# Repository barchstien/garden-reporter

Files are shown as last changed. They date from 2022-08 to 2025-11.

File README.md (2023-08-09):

[TOC]

# Overview
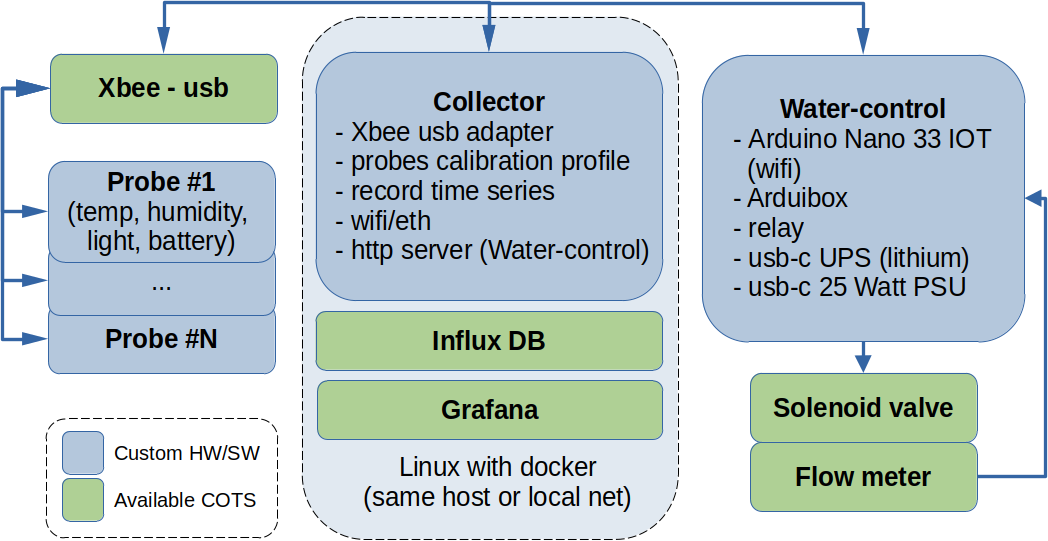
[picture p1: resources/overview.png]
probe overview


Collect data about the garden (soil humidity, luminosity and temperature), that is gathered via xbee link to the collector, for storage and visualisation.

Control and measure water flow. It flows when it is programmed to, or when manually triggered for a set duration.

Xbee modules are configured to :
 - cycle sleep to probe every 15min and stay ON for around 100 msec
 - send data to the collector

## UI and Configuration
 * Collector is configured via YAML, see [collector](/collector/) folder
 * Probes are configured when deployed, by uploading the profile (see profile*.xpro files)
 * Visulisation via Grafana
 * Water-control polls the set program every time it reports water flow
 * Water flow program is configured via web UI

# Probe
More doc about probe in [probe/](/probe)

# Collector
More doc about collector in [collector/](/collector)

# Water-control
More doc about water-control in [water-control/](/water-control)

# grafana-dashboards
Collection of grafan dashboards, exported as JSON, [here](/grafana-dashboards)

# resources
Images and diagrams

# IRL
The system has been running as a prototype since autumn 2022. Thought, after 2 months, the deployed probes started to randomly block, ie not wake up anymore, until it was rebooted. It got fixed only after changing the sleep switch (mosfet) from low side to high side. Cutting the low side was leading some voltage values to go beyond Xbee specs.

The v2 probe have been running since early february 2023. Two other probes have been deployed in mid-february and mid-april 2023. As of end of july 2023, they all perform within nominal parameters.

So far, I have used a COTS water programmer (jardibric PNR16). Which has been working fine. Thought it cannot be programmed to water at a chosen time, nor can it be easily triggered randomly without messing with the set program.

Water flow is also measured using a mechanical water counter found in the local hardware store.

## Visualisation
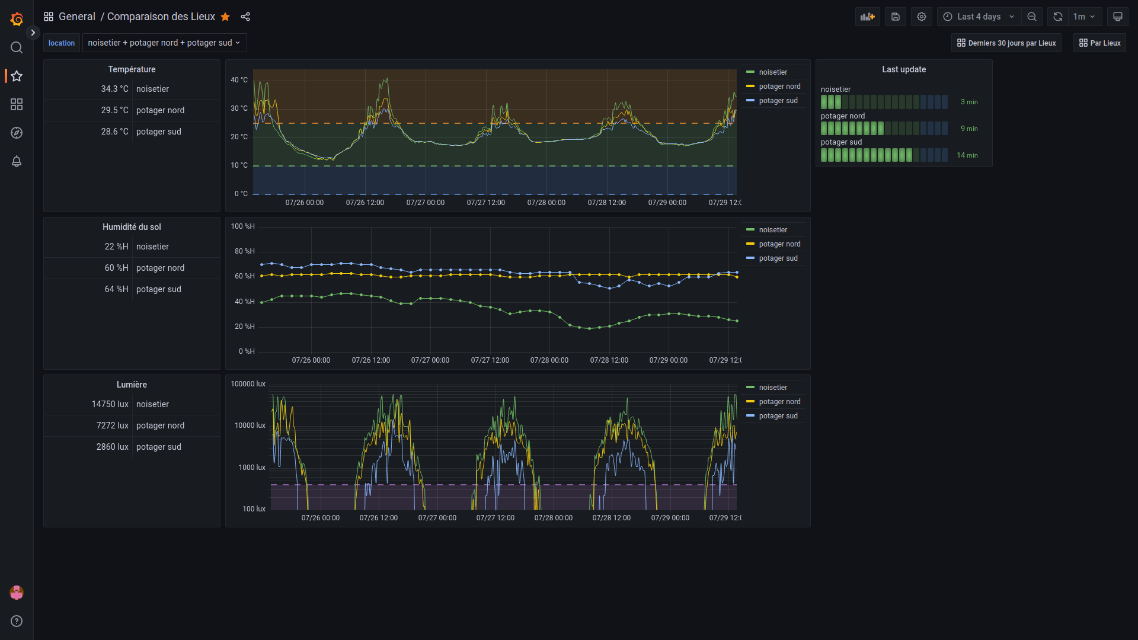
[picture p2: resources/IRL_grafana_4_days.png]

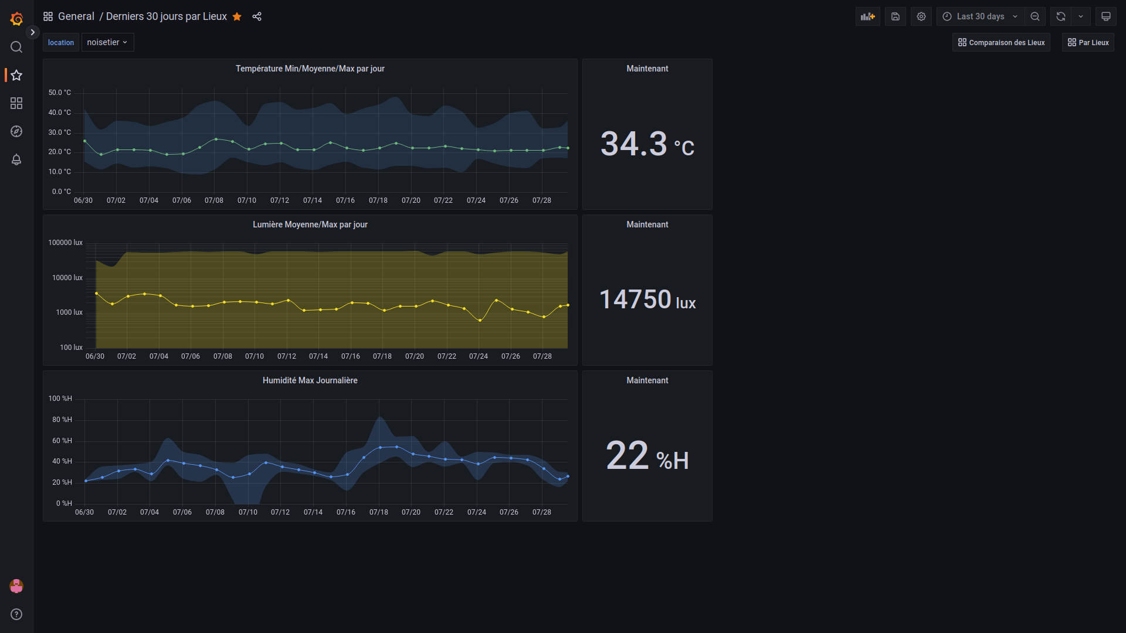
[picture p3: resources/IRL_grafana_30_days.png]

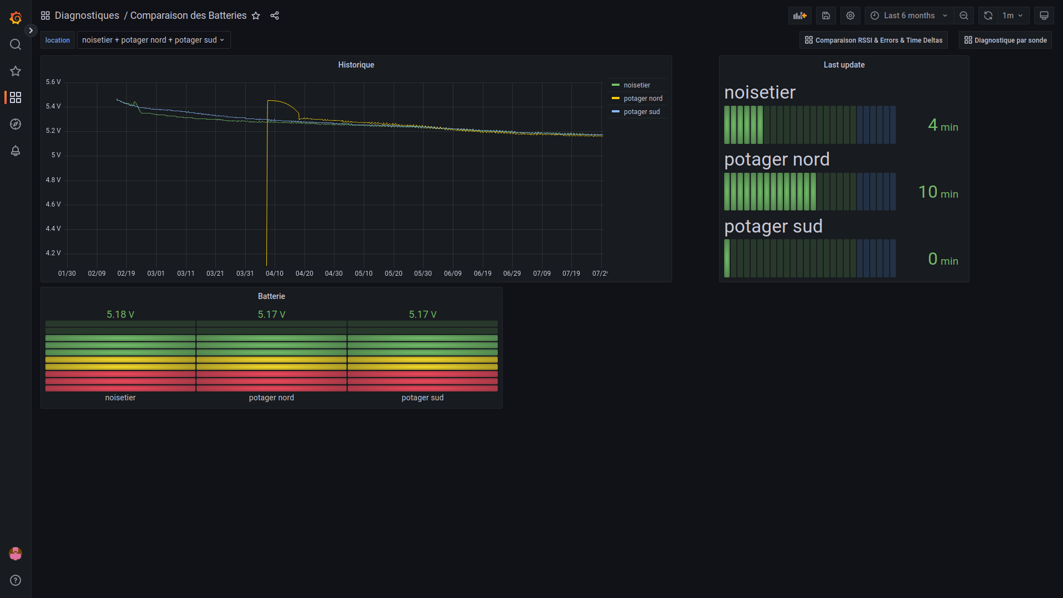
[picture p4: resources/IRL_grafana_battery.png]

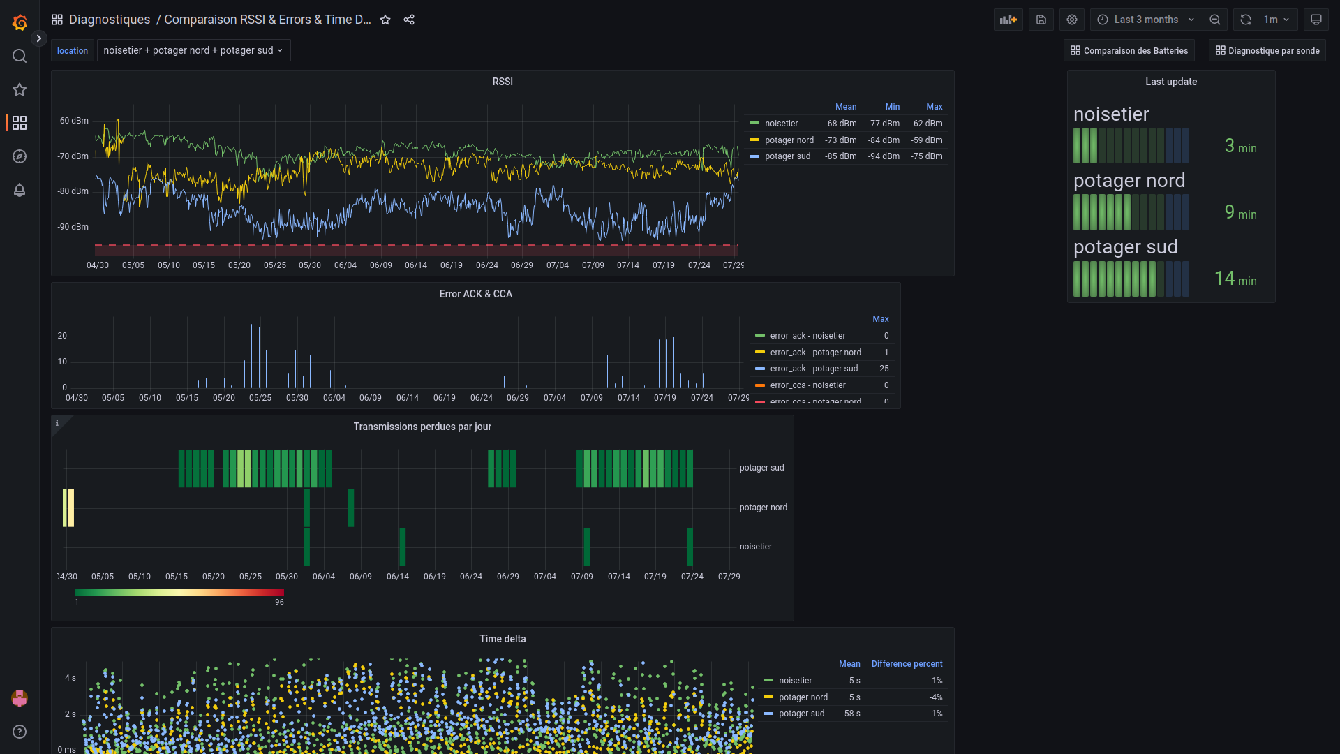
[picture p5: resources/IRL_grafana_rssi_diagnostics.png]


## Probe
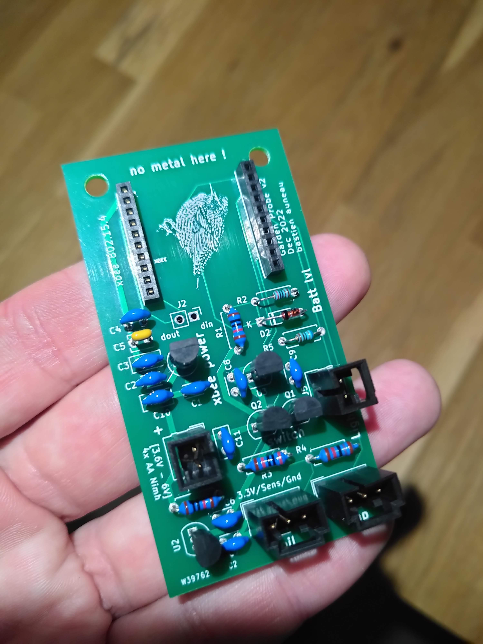
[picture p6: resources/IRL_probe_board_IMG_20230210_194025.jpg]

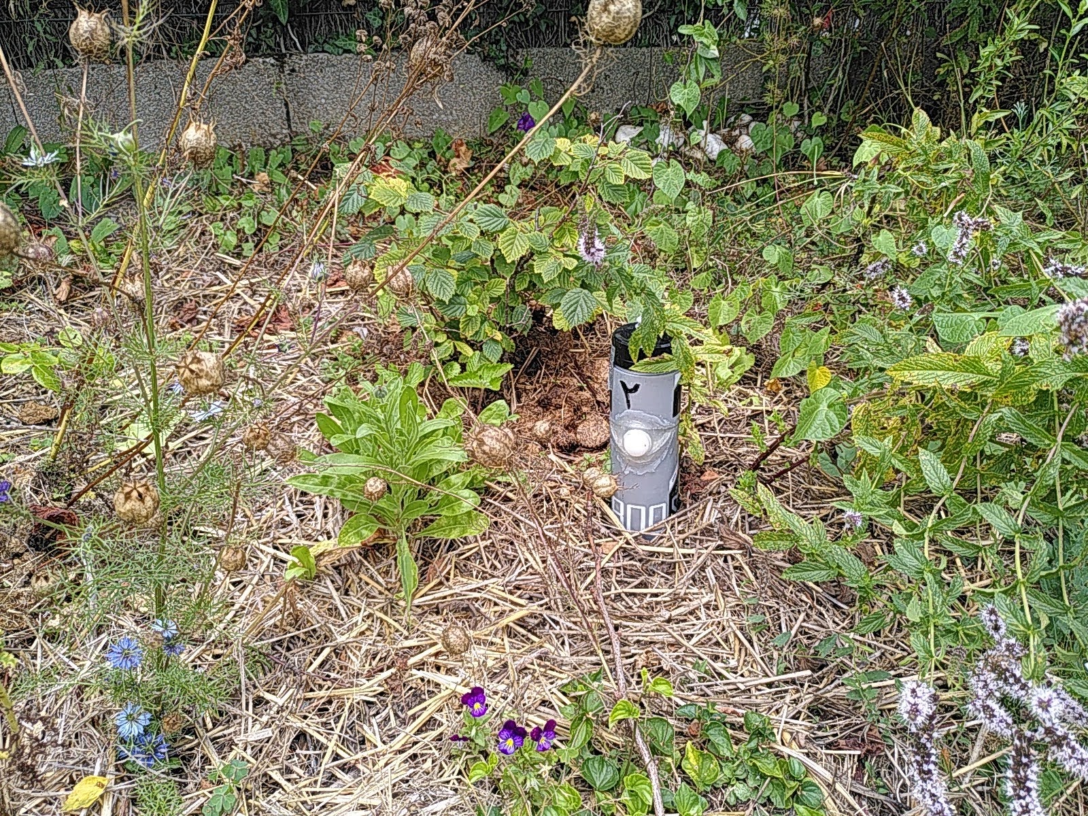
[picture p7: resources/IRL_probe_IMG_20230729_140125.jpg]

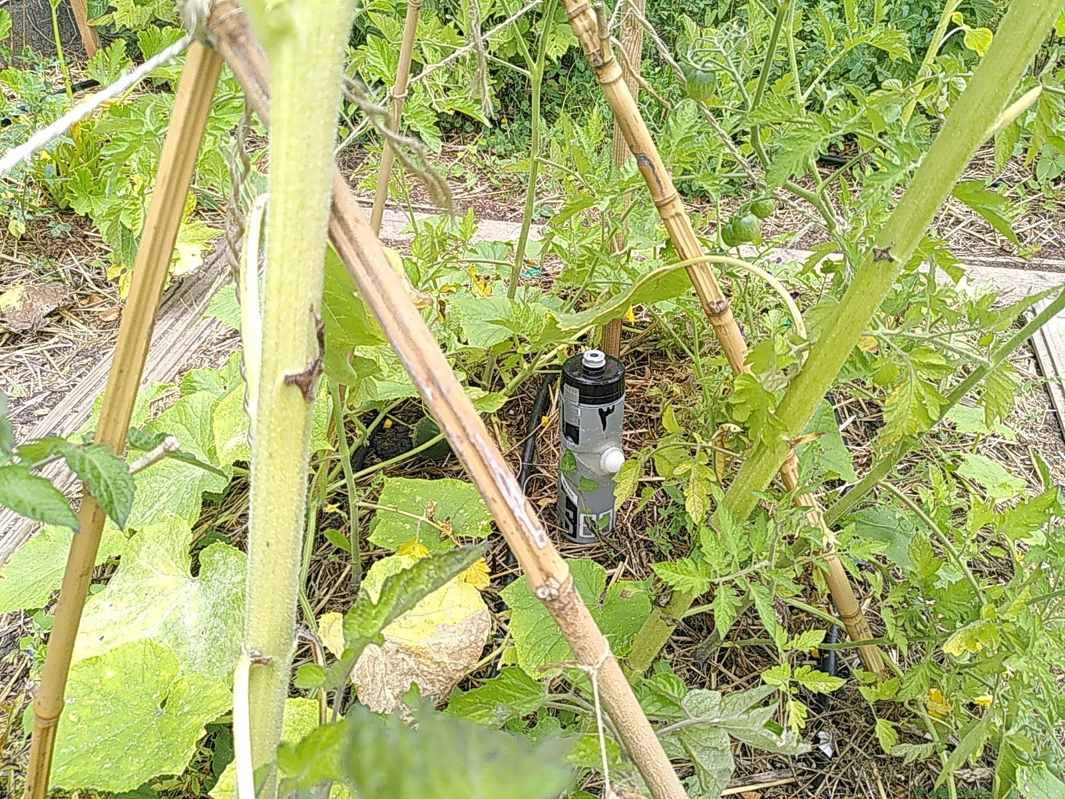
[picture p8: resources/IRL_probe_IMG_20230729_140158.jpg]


## Collector
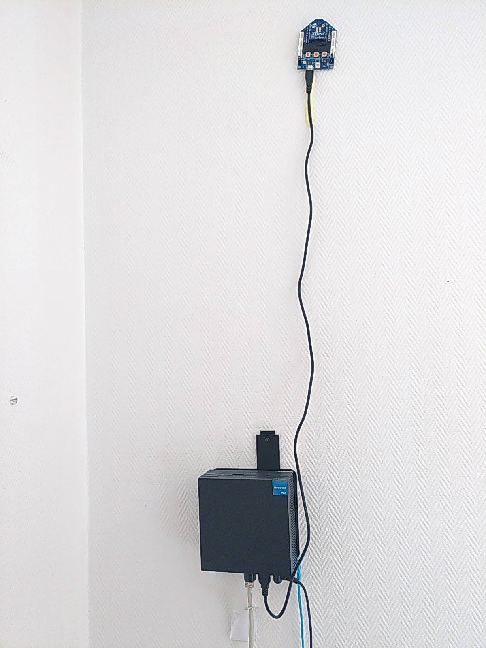
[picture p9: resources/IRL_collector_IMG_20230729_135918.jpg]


## Water-control
Coming soon

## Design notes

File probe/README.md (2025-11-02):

# Overview
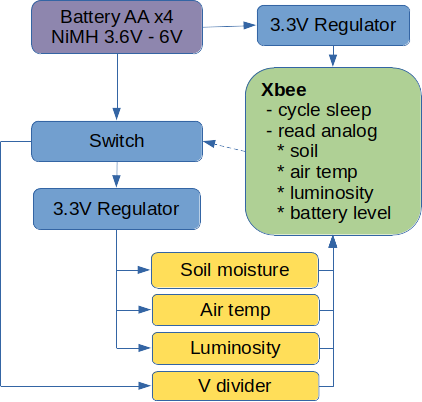
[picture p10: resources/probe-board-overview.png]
probe overview


## Features
 - Probe for :
   - soil humidity
   - air temperature
   - luminosity
   - battery level
 - 6 month+ battery (1 year). See **probe-board-power-use.ods**
 - Report to collector
   - via xbee 2.4GHz 802.15.4
   - every 15min using cycle sleep

Kicad files are in **probe/kicad** folder  
Components datasheet are in **probe/datasheet** folder  

## Board 3d view
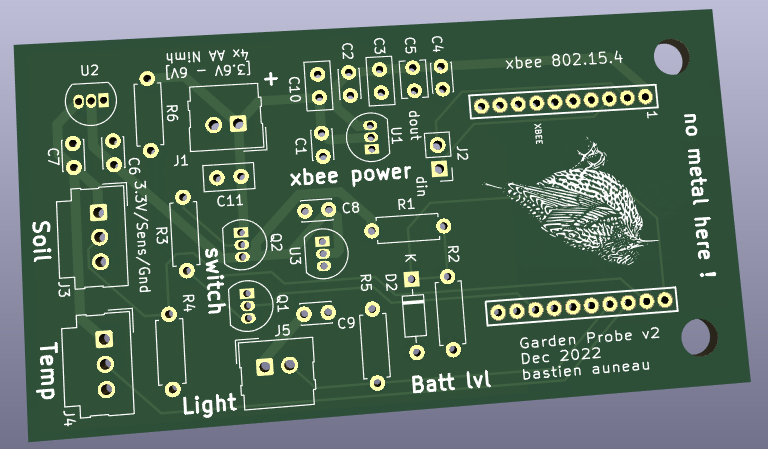
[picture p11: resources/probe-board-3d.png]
probe pcb 3d


# Mechanic and water consideration
 - case should be wateproof
   - plastic bottles are inexpensive and water proof
     - bottom is filled with gravel for stability and in case of leak
   - sensors are attached to case
   - wires from sensors to probe board are water resistent
     - use plumbing goo/joint/paste
   - sensors are environment protected :
     - luminosity is already in epoxy case, wire nail polished
     - temp and wires are nail polished
     - soil moisture bottom is (home made) epoxy coated (water + abrasive)
     - soild moisture top is nail polished

# Components
**Note :** [XXX-XX] : mouser order number

## Xbee
 * XB24CAPIT-001, TH, s2c 802.15.4 [888-XB24CAPIT-001]
    - give 1uF and 8pf cap on supply
    - good keepout (bigger better, no gnd plane up), for pcb antenna
 * usb adapter
    - usb explorer board from sparkfun WRL-11812 [474-WRL-11812] 26.33E
    - dfrobot DFR0050 [426-DFR0050] 18.95E

## Switch
 * TN0702N3-G, can switch 20V, on at 1V, 0.1uA stdby  
   1.53E [689-TN0702N3-G]  
 * Use flywheel diode to protect mosfet from switched inductive load  
   SB130 [637-SB130]
 
## Battery 
 * 4x AA Nimh 2000mAh low self-discharged
   - Accus hybrides Aeonium - 2100mAh 8E for 4, 85% after 1 year
   - Energizer accu recharge extreme 2000mAh 8.6E for 4
 * 4x battery holder 58x31x28 12BH343D-GR [12BH343D-GR]
   OR 534-2476 with snap-on ?  
 Nimh nominal/min/max voltage 1.2/0.9/1.5  
 with 4 cells 4.8/3.6/6V 

## 3.3V voltage regulator
 * MCP1700-3302E/TO 0.5E [579-MCP1700-3302E/TO]  
   Vin 2.3 to 6V, Vdrop typical 178mV, max 350mV  
   250 mA max output  
   Use 1uF co at output (and 1 at input ?)  
 
## Soil moisture sensor
Capacitor sensor  
  * SEN0193 DFRobot 7.9E [426-SEN0193]  
   |--> Protect with nail polish
   |--> been using that one at first. Wire wares off with UV  
        nail polish coating seams to hold fine after 1.5 year  
  * SEN0308 DFRobot 15E [https://wiki.dfrobot.com/Waterproof_Capacitive_Soil_Moisture_Sensor_SKU_SEN0308]  
   |--> Now uses that one, goes deeper, better wire, only nail polish coat the PCB edge
   |--> Use extra 55KOhm in serie of signal, solder in wire  
        This gives ADC values around [75; 800]  
  * 3.3V 5mA  
  * **Warning** some cheapper alternative exists but aren't documented, nor reliable  

## Temp sensor
 * TMP36GT9Z [584-TMP36GT9Z] 1.81E  
   Must add O.1uF cap, very close to device, ie on wire

## Photo transistor
 * TEPT5700 [782-TEPT5700]  
   Use with 5K resistor for outside use with diffuser, measure U, then I = U/R  
   From I, get Lux, using calibration with a ref lux meter  
 The value of R will set the sensibility and saturation level  
 Use with a diffuser, to mitigate the effect of the angle towards the light source  
 
 For inside use, use a higher R value. 
 Aiming 5000 Lux max inside, which is 1/10 of outside max use
 Outside uses 5K --> use 50K --> only have 2x 20K

## Battery level sensor
 * Add battery level check with voltage divider  
   with 2x 10K resitor 1%  
   with zener diode 1N4620 3.3V, [610-1N4620BK]

## Connector
 * sensor to board, 3ways
  - 70543-0002 [538-70543-0002] pcb straigth header  
    70543-0107 for even more gold plating !
  - 79758-0011 [538-79758-0011] crimped wire, 30cm, 22awg
  - 50-57-9403 [538-50-57-9403  ] cable mount
 * battery to board, same with 2 pins
   [538-70543-0106]
 * Use kicad Molex_SL_171971
 
## Case
 * bicycle bottle, ~750mL, 20cm high, 7cm diameter

## Various
 * R 10K 1% metal film : [603-MFR-25FRF5210K]
 * c 10uF ceramic : [710-860010472002] 25VDC 85degC max
 * C 1uF ceramic : [810-FG18X7R1E105KRT0] 25VDC
 * c 8.2 pF ceramic : [80-C315C829D2G] 200VDC

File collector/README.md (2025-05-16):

# Introduction
The collector receives data from probes via an USB/Serial connection to an XBEE s2c 802.15.4.
Then interprets the data and apply calibration, on a per probe basis.
Finally it records the data in influxdb.
The data that are recorded are :
 * probe id (64 bit source address)
 * rssi (RF link level), from both sites
 * battery level
 * soil moisture
 * temperature
 * light

The collector allows to connect to a TCP port, that can be mounted to a local virtual serial port, allowing to use XCTU (Xbee official utilities) via the network. More in [TCP Serial chapter](#tcp-serial)

The data flow follows
```
Xbee --> Serial/USB --> python3 --> influxdb
```

**TODO** a nice diagram of collector guts

## Features
 - Waits for probes (Xbee) to wake up, and trigger sampling
 - Apply calibration
 - Store collected data to influx db
 - Keep a list of probes and their profiles
 - Water Web Server, for Human interaction, and water-control

## Probe profile
Probes have unit specific characteristics which need to be stored at the collector level :
 - Soil moisture dry/water values. Those values change from probe to probe, even more with (home made) epoxy coating
 - xbee identifier
 - placement
 - ganeric comments (dates for commissioning of probe and batteries)

## Design
 - xbee usb module
 - low power fanless PC (ASUS Mini PC PN41)
 - influxdb storage
 - grafana visulisation
 - python 3 (pipenv)
 - full yaml config

## Calibration
It may use a formula from datasheet or a manual calibration
 * moist : get dry/immerge value, gives linear ratio as %
 * temperature : from datasheet deg = V*100 - 50
 * Compare with a calibrated lux meter
 * battery voltage divider = 6

## Water Web Server
It has 2 use cases :
 * For Human, to setup auto-watering, and get short status of water-control
 * For water-control, to poll config and push status

### water-control /report
water-control makes a GET report to **/report**
GET params are :
 * last scheduled watering (?)
 * next schedule watering
 * water liter value
 * watering now
 * uptime
Returns **application/json** with params:
 * 'period_day_value': the period at which watering occurs
 * 'start_time_hour_minute_value': watering start time
 * 'duration_minute_value': duration of the watering in minutes
 * 'sec_since_1970': current time in sec since EPOCH

### water-control /debug
**Warning: DEPRECATED**
water-control makes a GET debug to **/debug**, with params :
 * 'debug': text

# TCP Serial
A TCP port is open to allow taking over the serial for a specific device MAC.
It first wait for the target to wake up, and disable cycle sleep
It then mounts the tcp connection as a pty, to open with xctu
When the tcp connection is broken, the device is put back to cycle sleep mode, and the pty is unmounted
```bash
pipenv run python3 ./source/serial_tcp_client.py

# run XCTU
/opt/Digi/XCTU-NG/app
```

# Deploy
Use docker compose with compose.yaml
It's about doing :
```bash
docker compose up --build -d
```
With extra few steps for 1st time deploy 

1. create env_file  
    Used to set some const and secrets  
    **WARNING** need to rebuild container (or maybe delete ?)... at least restart isn't enough !
    expects **env_file** as :
    ```bash
    # used by collector
    export INFLUX_TOKEN=should-be-generated-with-influx-auth-later
    
    # used by influxdb and collector
    export ORG=potager-org
    export BUCKET=potager-bucket
    
    # used by influxdb
    export USERNAME=potager
    # 8 character minimum
    export PASSWORD=potagerpotager
    ```

2. start/config influxdb
    ```bash
    # start influxdb
    docker compose up influxdb -d
    
    # setup influxdb
    source env_file
    docker exec garden-reporter-influxdb influx setup \
      --username $USERNAME \
      --password $PASSWORD \
      --org $ORG \
      --bucket $BUCKET \
      --force
    
    # generate token
    docker exec garden-reporter-influxdb influx auth create --all-access --org $ORG
    # copy/paste token to env_file
    # list token with 
    docker exec garden-reporter-influxdb influx auth list
    ```
    See [influxdb docker official](https://hub.docker.com/_/influxdb)

3. start/config grafana
   ```bash
   docker compose up grafana -d
   ```
   Got to web ui http://192.168.1.X:3000  
   Default pass is admin:admin  
   Add :
   - an influxdb data source using the generated TOKEN  
     - use the real ip (not localhost) in url
     - Disable all Auth, only fill the token lower in the page
   - a user to access on daily basis
     - make the user admin to allow creating dashboard
  **Warning** : export JSON modules to be used externally

4. create/update collector and water-web-server config 
    Update env_file with influxdb token
    ```bash
    docker volume create garden-collector
    docker run --rm -it -v $(pwd):/tmp/garden-collector -v garden-collector:/var/lib/garden-collector ubuntu cp /tmp/garden-collector/collector.yaml /var/lib/garden-collector/
    docker run --rm -it -v $(pwd):/tmp/garden-collector -v garden-collector:/var/lib/garden-collector ubuntu cp /tmp/garden-collector/water-web-config.yaml /var/lib/garden-collector/
    # set rights
    docker run --rm -it -v garden-collector:/var/lib/garden-collector ubuntu chown -R 1000:1000 /var/lib/garden-collector
    ```

5. start collector
    ```bash
    docker compose up collector --build -d
    ```

# Maintenance
```sh
# compose and build Docker file
docker compose up collector --build -d
docker compose restart collector

# influxdb token
docker exec garden-reporter-influxdb influx auth list

# collector config
# copy yaml TO container (collector needs restart, not water web server)
docker cp water-web-config.yaml garden-reporter-collector:/var/lib/garden-collector/
docker cp collector.yaml garden-reporter-collector:/var/lib/garden-collector/
# copy yaml FROM container
docker cp garden-reporter-collector:/var/lib/garden-collector/water-web-config.yaml ./
docker cp garden-reporter-collector:/var/lib/garden-collector/collector.yaml ./
```

# Backup
TODO, use docker compose too !!!

# Dev notes

## xbee
Configure xbees with XCTU
Install and launch XCTU config SW
```bash
# launch XCTU
/opt/Digi/XCTU-NG/app

# serial tcp
/tmp/garden0
```
probe XCTU profile has sleep disable by default, it has to be enabled manually  
**WARNING** When sleeping, got to force reboot to reconnect, hard to reconnect  
**INFO** Using serial/TCP collector disable/re-enable sleep mode on tcp client connect/disconnect  

Load .xpro profiles for collector, and for each probe

### xbee config notes
 * setup End Point as :
   - Cycle Sleep
   - IR = 0
     millisec between samples. IR = 0 means no auto-sampling
   - keep SO (Sleep Option) default
     default 0b00, 0b01 disable wakeup poll, 0b10 no sample on wakeup
   - Use 64bit address, coz 64bit address is required to send config
     MY should be set to 0xFFFF
   - endpoint destination (DH and DL) should be set to collector MAC
   End Point send a sample on wake up
   Use this as a signal
   0x82 (RX (Receive) Packet 64-bit Address IO)
 * use RSSI from wake up sample frame
 * send remote AT cmd 
   - IS to get samples
   - DB for last RSSI
     ! Different from pervious RSSI
   - EA ACK failure cnt
     ! For collector too
   - EC CCA failure cnt
     ! collector too
 * 0x17 Remote AT Command Request, p137
 * 0x97 Remote AT Command Response, p155
 * 0x82 64-bit I/O Sample Indicator, p144
 * Channel (CH) B seams to have better RSSI

## Python Collector
Use **pipenv** to manage virtual env and packages
```bash
# load Pipfile
pipenv install
# load ./Pipfile.lock
pipenv install --ignore-pipfile
# add --dev for dev only pkg
# lock (save) current env to Pipfile.lock
pipenv lock

# add more pkg with
# use --dev if it's a dev only dep
pipenv install|uninstall blabla

pipenv shell
pipenv run <cmd>
```

### influxdb token and secrets
```bash
# export influx API token
# env_file line format is foo=bar
source env_file
# run
pipenv run python3 collector.py
```

### dev
```bash
# run detached
nohup pipenv run python3 main.py > log.txt &

# fwd serial to tcp
socat tcp-listen:8087,reuseaddr file:/dev/ttyUSB0,nonblock,b9600,raw,echo=0 
# virtual serial
socat pty,link=/tmp/garden0,raw,echo=0 tcp:192.168.1.66:8087

# standalone/debug water web server
# from collector folder
pipenv run python -u ./source/water_web_server.py
```

## influxdb
**TODO** Use docker compose for that !!!!  
```bash
# config with
docker exec -it garden-reporter-influxdb influx

# backup
# from bastien@gnome-server:~/dev/garden-reporter/collector$ 
bckdate=$(date +%y_%m_%d-%H_%M_%S)
docker exec -it garden-reporter-influxdb bash -c "influx backup -b $BUCKET -t $INFLUX_TOKEN /tmp/$bckdate/"
docker cp garden-reporter-influxdb:/tmp/$bckdate ./backup_influxdb/

# restore
docker cp ./backup_influxdb/$bckdate garden-reporter-influxdb:/tmp/backup
# --full also restores dash boards, tokens, etc
docker exec -it garden-reporter-influxdb bash -c "influx restore /tmp/backup --full"

```

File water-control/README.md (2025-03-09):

# Water control
Control a solenoid valve, measure the outgoing water flow, report and take order using wifi + http GET

# HW
 * Arduino nano 33 iot (wifi)
   - [datasheet](../water-control/datasheet/arduino-nano-33-iot-datasheet.pdf)
   - [SAM-D21 (chip) datasheet](../water-control/datasheet/SAM-D21DA1-Family-Data-Sheet-DS40001882G.pdf)
 * Arduibox (DIN RAIL + power supply + PCB)
   - [Datasheet](../water-control/datasheet/Datasheet_ArduiBox_Rev_B-2.pdf)
   - [Construction manual](../water-control/datasheet/Construction_manual_ArduiBox_rev_B-4.pdf)
 * H bridge (N-mos)
   - commercial name : DRV8874 Single Brushed DC Motor Driver Carrier
   - [Official doc](https://www.pololu.com/product/4035)
   - [board schematic](../water-control/datasheet/drv887x-single-brushed-dc-motor-driver-carrier-schematic.pdf)
   - [drv8874 datasheet](../water-control/datasheet/drv8874.pdf)
 * DEPRECATED - hard to drive, blaming too low pressure
   Rainbird electro valve with 9V solenoid
   - 100-DVF
   - Rain Bird TBOS latching solenoid (does datasheet exists ?)
     Model ? TBOSPSOL or K80920  
 * Ball Valve 
   Normally closed, closes using a spring once power is off 
   - can control it using H-bridge meant for electrovalve
   - no need for battery anymore
   - TF20-B2-B 9-24VDC 
   - 3sec open/close motor stop when fully opened
 * Power supply
   - HDR-30-15
   - 15V 2A DIN rail
 * Adafruit DS3231 breakout board
   - [Official doc](https://www.adafruit.com/product/3013)
   - Note SAMD31 does have an RTC, but not crystal, so no good stability
 * Interface
   - LED
   - Start watering push button
   - 3 button to code 3 bits (x15min, to set watering duration)
   - On/Off button, forbid water use when off

## Schematics
TODO
ALSO check that rplacing 9V by 12V is fine !!!!!!!!!!!
Input power (now 9V) goes to :
 - arduibox voltage regulatr that takes 9 to 30 VDC
 - power rails of H-bridge takes 4.5 to 37V DC
|--> should be all fine !

## Power use
| Function  | Consumption mA  |
|--:|---|
|delay |25 |
|wifi connect |45 to 85 |
|wifi low power mode |45 to 55 |
|wifi end |25 |
|LowPower idle/sleep/deep |19
|coil driver no load |2.5
|5V reg no load |3.5
|flow meter alone |2

# SW
using Arduino IDE, source is in [water-control](./water-control)  
Requires Arduino Libraires (to install with IDE) :  
 * ArduinoHttpClient (easy http GET)
 * ArduinoJson (Json http response)
 * Arduino_Low_Power (to confirm, to keep power usage to min)
 * RTCLib for Adafruit DS3231 breakout board
 * Time (unix to date/time, local time sync)
 * WiFiNINA (wifi connection + web client)

# Interface
```

|------1-2-3-4-5-6---7-8-9-10-11-12---|
|                                     |
|                                     |
|                                     |
|    Arduibox layout seen from top    |
|                                     |
|                                     |
|                                     |
|-----------------------------Gnd-15V-|
```
**Note:** [Pin #] as on drawing
| Pin # | Function |
|--:|---|
|1| batt sense |
|2| 3.3V |
|3| flow trig |
|4| gnd |
|5| LED (pwm) |
|6| start trig |
|||
|7| allow water |
|8| bit 2 |
|9| bit 1 |
|10| bit 0 |
|11| valve 0V |
|12| valve +15V |

## Button interface
```
|-1-2-3____4-5-6-7-|
|                  |
|                  |
|                  |
|                  |
|------------------|
```
**Note:** [Pin #] as on drawing
| Pin # | Function |
|--:|---|
|1| gnd |
|2| led |
|3| start trig |
|||
|4| allow water |
|5| bit 2 |
|6| bit 1 |
|7| bit 0 |

# TODO
 * Use RTC board square wave output at 1KHz, to get better msec precision for valve pulse ?
   |--> require to unmount from arduibox to solder new pin...
   |--> easy to setup 
   |--> only enable/use when doing valve pulse ?
        OR ? Could totally replace millis() ?
        With 48MHz M0 and 1024Hz sqw wave, it means 1 interrupt every 48K cycles... not bad
 * save in RTC flash (alarm), next epoch time and perdio/duration
   |--> if power comes back, and server isn't up <--- no so likely..
 * suspecting manual trigger to be canceled if can't wifi connect to server

# Notes
file:///home/bastien/while-true/common/garden-reporter/water-control/index.html?period=1&start-time=12%3A30&duration=66

# Bibliography
 * [Arduino-Nano-33-IoT-Ultimate-Guide](https://github.com/ostaquet/Arduino-Nano-33-IoT-Ultimate-Guide)
 * [Official](https://docs.arduino.cc/hardware/nano-33-iot)

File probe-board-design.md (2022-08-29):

# Overview
probe overview

**Note :** [XXX-XX] : mouser order number

# Components
## Xbee
 * XB24CAPIT-001, TH, s2c 802.15.4 [888-XB24CAPIT-001]
    - give 1uF and 8pf cap on supply
    - good keepout (bigger better, no gnd plane up), for pcb antenna
 * usb adapter
    - usb explorer board from sparkfun WRL-11812 [474-WRL-11812] 26.33E
    - dfrobot DFR0050 [426-DFR0050] 18.95E

## Switch
 * TN0702N3-G, can switch 20V, on at 1V, 0.1uA stdby
   1.53E [689-TN0702N3-G]
   TODO add Resistor between gate and Gnd, to help discharge ?
   |---> Or not ? coz xbeen will drive it low
   |---> keep un-populated pad for resistor
 * Use flywheel diode to protect mosfet from switched inductive load
   SB130 [637-SB130]
 
## Battery 
 * 4x AA Nimh 2000mAh low self-discharged
   - Accus hybrides Aeonium - 2100mAh 8E for 4, 85% after 1 year
   - Energizer accu recharge extreme 2000mAh 8.6E for 4
 * 4x battery holder 58x31x28 12BH343D-GR [12BH343D-GR]
   OR 534-2476 with snap-on ?
 Nimh nominal/min/max voltage 1.2/0.9/1.5  
 with 4 cells 4.8/3.6/6V 

## 3.3V voltage regulator
 * MCP1700-3302E/TO 0.5E [579-MCP1700-3302E/TO]
   Vin 2.3 to 6V, Vdrop typical 178mV, max 350mV
   250 mA max output
   Use 1uF co at output (and 1 at input ?)
 
## Soil moisture sensor
 * Capacitor sensor
   SEN0193 DFRobot 7.9E [426-SEN0193]
   SEN0308 DFRobot 15E
   3.3V 5mA

## Temp sensor
 * TMP36GT9Z [584-TMP36GT9Z] 1.81E
   Must add O.1uF cap, very close to device, ie on wire

## Photo transistor
 * TEPT5700 [782-TEPT5700]
   Use with 10K resistor, measure U, then I = U/R
   From I, get Lux

## Battery level sensor
 * Add battery level check with voltage divider 
   with 2x 10K resitor 1%
   with zener diode 1N4620 3.3V, [610-1N4620BK]

## Connector
 * sensor to board, 3ways
  - 70543-0002 [538-70543-0002] pcb straigth header
    70543-0107 for even more gold plating !
  - 79758-0011 [538-79758-0011] crimped wire, 30cm, 22awg
  - 50-57-9403 [538-50-57-9403  ] cable mount
 * battery to board, same with 2 pins
   [538-70543-0106]
 * Use kicad Molex_SL_171971
 
## Case
 * bicycle bottle, ~750mL, 20cm high, 7cm diameter

## Various
 * R 10K 1% metal film : [603-MFR-25FRF5210K]
 * c 10uF ceramic : [710-860010472002] 25VDC 85degC max
 * C 1uF ceramic : [810-FG18X7R1E105KRT0] 25VDC
 * c 8.2 pF ceramic : [80-C315C829D2G] 200VDC

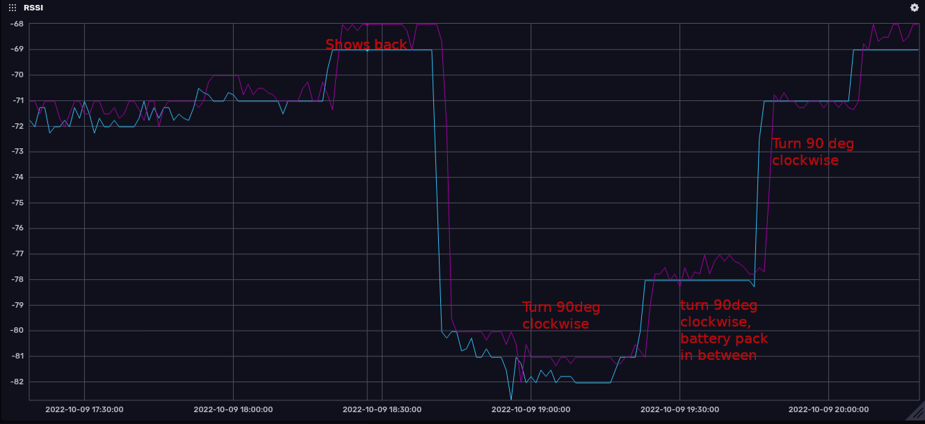
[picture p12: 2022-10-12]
resources/garden_reporter_rssi_vs_orientation_commented.png

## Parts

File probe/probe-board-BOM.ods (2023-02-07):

Designator | Quantity | Designation | Mouser | Farnell | Comments
 | 1 | xbee | 888-XB24CAPIT-001
JP1 | 2 | xbee socket | 710-62001011821
J1, J5 | 2 | 70543-0106 | 538-70543-0106 |  | molex socket 2 rows
J3, J4 | 2 | 70543-0002 | 538-70543-0002 |  | molex socket 3 rows
D2 | 1 | 1N4620 | 610-1N4620BK |  | Zener
C1, C2, C4, C6, C7, C8, C9 | 7 | 1uF | 810-FG18X7R1E105KRT0
C3, C10, C11 | 3 | 10uF | 810-FG18X5R1E106MR06
C5 | 1 | 8.2pF | 80-C315C829D2G
U1,U2 | 2 | 3.3V Regulator | 579-MCP1700-3302E/TO | 1296588
U3 | 1 | 1.2V Regulator | 579-MCP1700-1202E/TO
Q1 | 1 | TN0702N3-G | 689-TN0702N3-G |  | N-mosfet switch
Q2 | 1 |  | 689-VP3203N3-G |  | P-mosfet switch
R1, R6 | 2 | 10K 1% | 603-MFR-25FRF5210K
R2 |  | 2K 1% | 603-MFR-25FRF522K
R3 |  | 20K | 603-MFR-25FRF5220K
R4 |  | 17K 1% | 603-MFR-25FTF52-17K
R5 |  | 68 1% | 279-LR0204F68R
Below are not on PCB
 | 1 | battery holder | 12BH343D-GR
 | 1 | soil moisture sensor | 426-SEN0193
 | 1 | temp sensor | 584-TMP36GT9Z
 | 1 | photo transistor | 782-TEPT5700
DEPRECATED
 | 11 |  | 538-79758-0011 |  | molex crimpd wires 30cm 22 AWG
 | 4 |  | 538-79758-0009 |  | 30cm red 18 AWG
 | 1 |  | 474-WRL-11812 |  | xbee usb

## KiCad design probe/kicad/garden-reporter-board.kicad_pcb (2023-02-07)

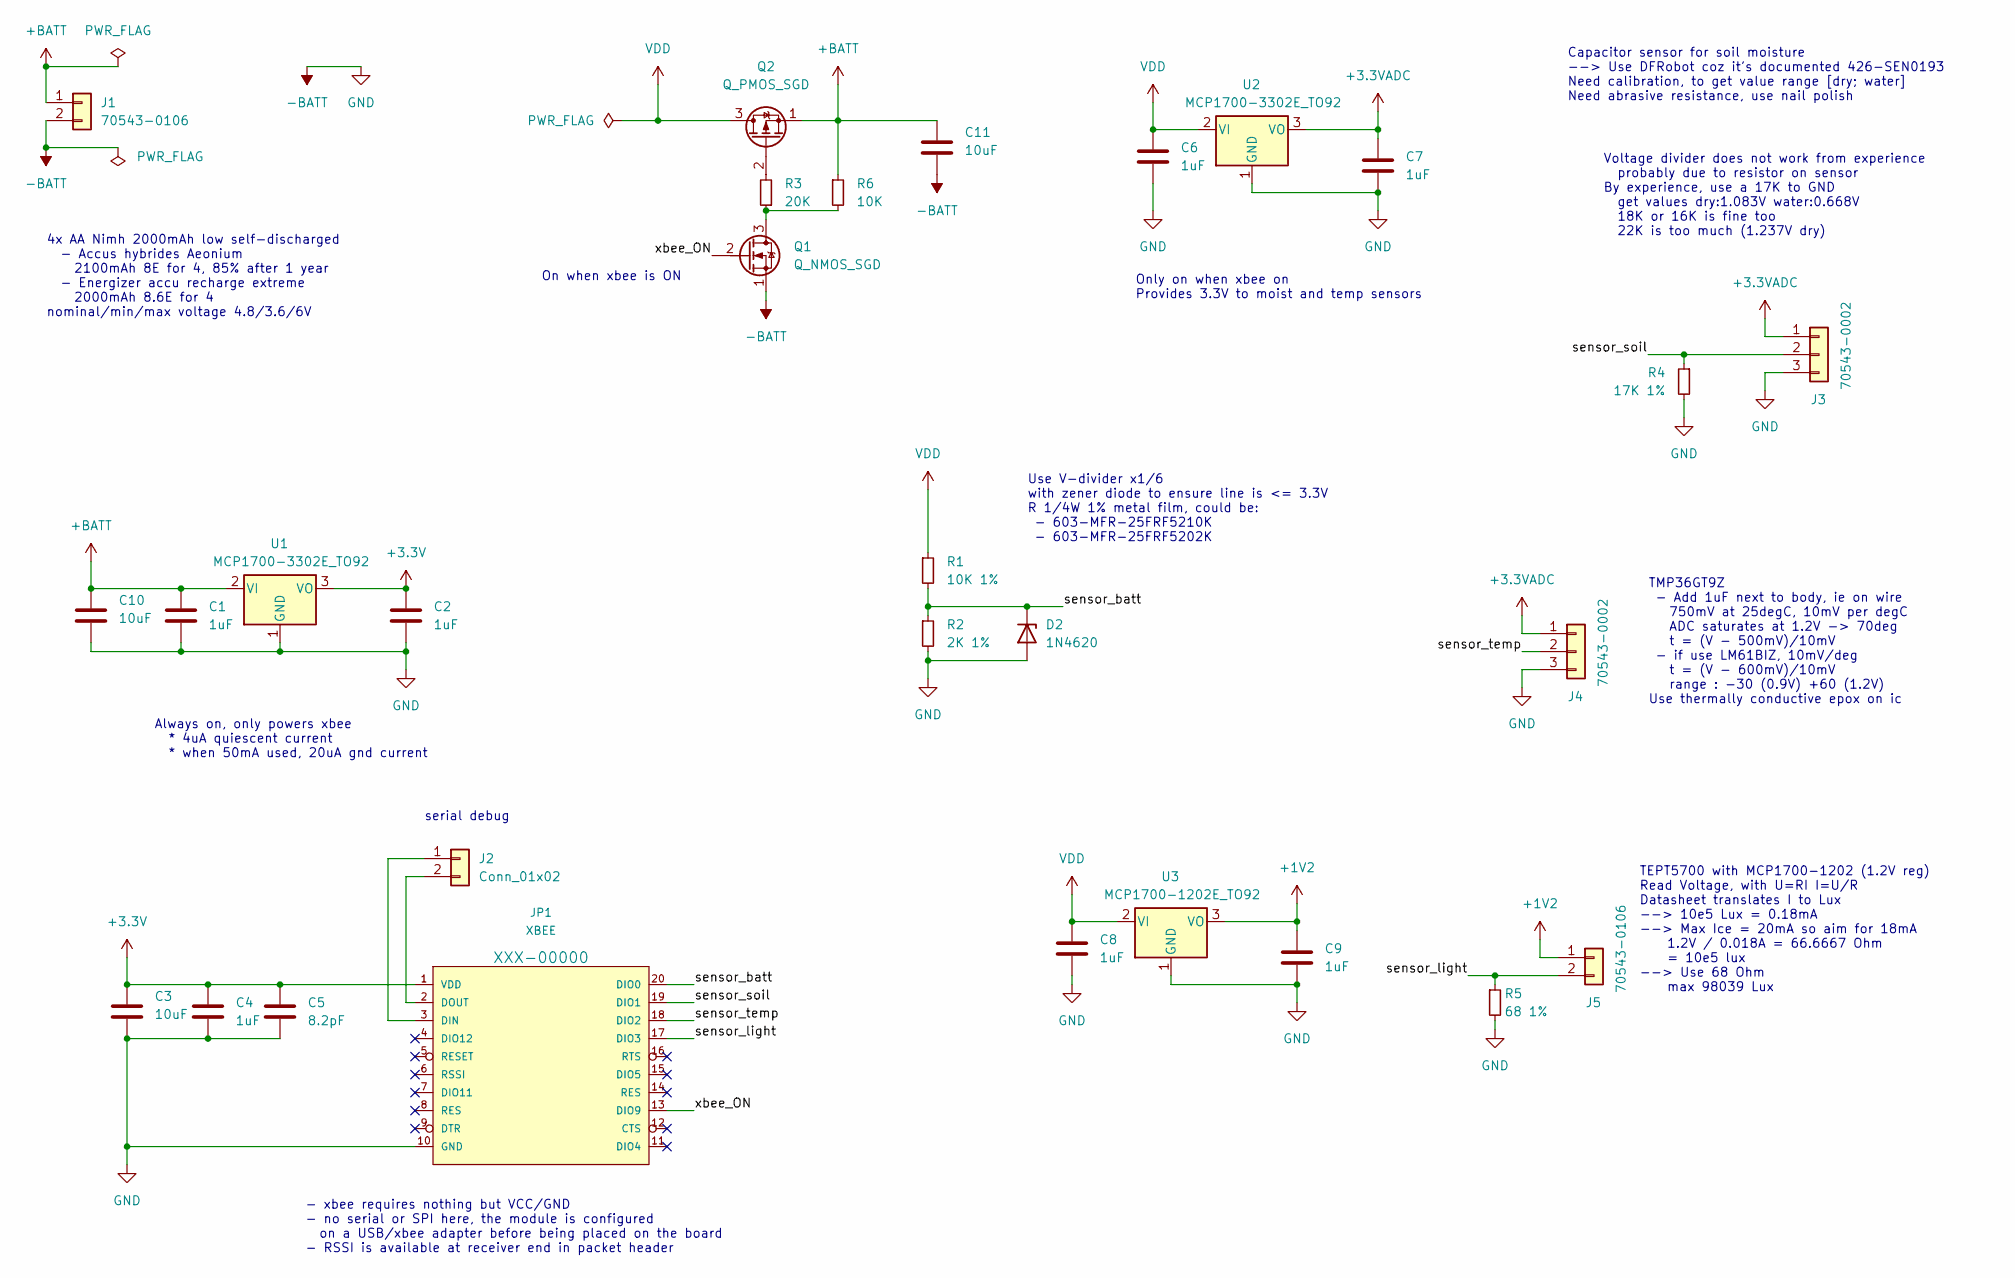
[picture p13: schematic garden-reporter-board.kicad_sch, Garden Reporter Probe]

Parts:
C1, C2, C4, C6, C7, C8, C9: 1uF; C_Disc_D3.0mm_W2.0mm_P2.50mm; mouser FG18X5R1H105KRT06
C3, C10, C11: 10uF; C_Disc_D5.0mm_W2.5mm_P2.50mm; mouser 810-FG18X5R1E106MR06
C5: 8.2pF; C_Disc_D3.8mm_W2.6mm_P2.50mm; mouser 80-C315C829D2G
D2: 1N4620; D_DO-35_SOD27_P7.62mm_Horizontal; mouser 610-1N4620BK
J1, J5: 70543-0106; Molex_SL_171971-0002_1x02_P2.54mm_Vertical; mouser 538-70543-0106
J2: Conn_01x02; PinHeader_1x02_P2.54mm_Vertical
J3, J4: 70543-0002; Molex_SL_171971-0003_1x03_P2.54mm_Vertical; mouser 538-70543-0002
JP1: XBEE; mouser 710-62001011821
Q1: Q_NMOS_SGD; TO-92_Inline; mouser 689-TN0702N3-G
Q2: Q_PMOS_SGD; TO-92_Inline; mouser 689-VP3203N3-G
R1: 10K 1%; R_Axial_DIN0207_L6.3mm_D2.5mm_P7.62mm_Horizontal; mouser 603-MFR-25FRF5210K
R2: 2K 1%; R_Axial_DIN0207_L6.3mm_D2.5mm_P7.62mm_Horizontal; mouser 603-MFR-25FRF522K
R3: 20K; R_Axial_DIN0207_L6.3mm_D2.5mm_P7.62mm_Horizontal; mouser 603-MFR-25FRF5220K
R4: 17K 1%; R_Axial_DIN0207_L6.3mm_D2.5mm_P7.62mm_Horizontal; mouser 603-MFR-25FTF52-17K
R5: 68 1%; R_Axial_DIN0207_L6.3mm_D2.5mm_P7.62mm_Horizontal; mouser 279-LR0204F68R
R6: 10K; R_Axial_DIN0207_L6.3mm_D2.5mm_P7.62mm_Horizontal; mouser 603-MFR-25FRF5210K
U1, U2: MCP1700-3302E_TO92; TO-92_Inline; mouser 579-MCP1700-3302E/TO
U3: MCP1700-1202E_TO92; TO-92_Inline; mouser 579-MCP1700-1202E/TO

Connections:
+1V2: C9.1, J5.1, U3.3 (VO)
+3.3V: C2.1, C3.1, C4.1, C5.1, JP1.1 (VDD), U1.3 (VO)
+3.3VADC: C7.1, J3.1, J4.1, U2.3 (VO)
+BATT: C1.1, C10.1, C11.1, J1.1, Q2.1 (S), R6.1, U1.2 (VI)
-BATT: C1.2, C2.2, C3.2, C4.2, C5.2, C6.2, C7.2, C8.2, C9.2, C10.2, C11.2, D2.2 (A), J1.2, J3.3, J4.3, JP1.10 (GND), Q1.1 (S), R2.2, R4.2, R5.2, U1.1 (GND), U2.1 (GND), U3.1 (GND)
/sensor_batt: D2.1 (K), JP1.20 (DIO0), R1.2, R2.1
/sensor_light: J5.2, JP1.17 (DIO3), R5.1
/sensor_soil: J3.2, JP1.19 (DIO1), R4.1
/sensor_temp: J4.2, JP1.18 (DIO2)
/xbee_ON: JP1.13 (DIO9), Q1.2 (G)
unnamed: J2.1, JP1.3 (DIN)
unnamed: J2.2, JP1.2 (DOUT)
unnamed: Q1.3 (D), R3.1, R6.2
unnamed: Q2.2 (G), R3.2
VDD: C6.1, C8.1, Q2.3 (D), R1.1, U2.2 (VI), U3.2 (VI)

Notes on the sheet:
- xbee requires nothing but VCC/GND - no serial or SPI here, the module is configured on a USB/xbee adapter before being placed on the board - RSSI is available at receiver end in packet header
Voltage divider does not work from experience probably due to resistor on sensor By experience, use a 17K to GND get values dry:1.083V water:0.668V 18K or 16K is fine too 22K is too much (1.237V dry)
Use V-divider x1/6 with zener diode to ensure line is <= 3.3V R 1/4W 1% metal film, could be: - 603-MFR-25FRF5210K - 603-MFR-25FRF5202K
Always on, only powers xbee * 4uA quiescent current * when 50mA used, 20uA gnd current
4x AA Nimh 2000mAh low self-discharged - Accus hybrides Aeonium 2100mAh 8E for 4, 85% after 1 year - Energizer accu recharge extreme 2000mAh 8.6E for 4 nominal/min/max voltage 4.8/3.6/6V
Only on when xbee on Provides 3.3V to moist and temp sensors
TMP36GT9Z - Add 1uF next to body, ie on wire 750mV at 25degC, 10mV per degC ADC saturates at 1.2V -> 70deg t = (V - 500mV)/10mV - if use LM61BIZ, 10mV/deg t = (V - 600mV)/10mV range : -30 (0.9V) +60 (1.2V) Use thermally conductive epox on ic
On when xbee is ON
Capacitor sensor for soil moisture --> Use DFRobot coz it's documented 426-SEN0193 Need calibration, to get value range [dry; water] Need abrasive resistance, use nail polish
serial debug
TEPT5700 with MCP1700-1202 (1.2V reg) Read Voltage, with U=RI I=U/R Datasheet translates I to Lux --> 10e5 Lux = 0.18mA --> Max Ice = 20mA so aim for 18mA 1.2V / 0.018A = 66.6667 Ohm = 10e5 lux --> Use 68 Ohm max 98039 Lux

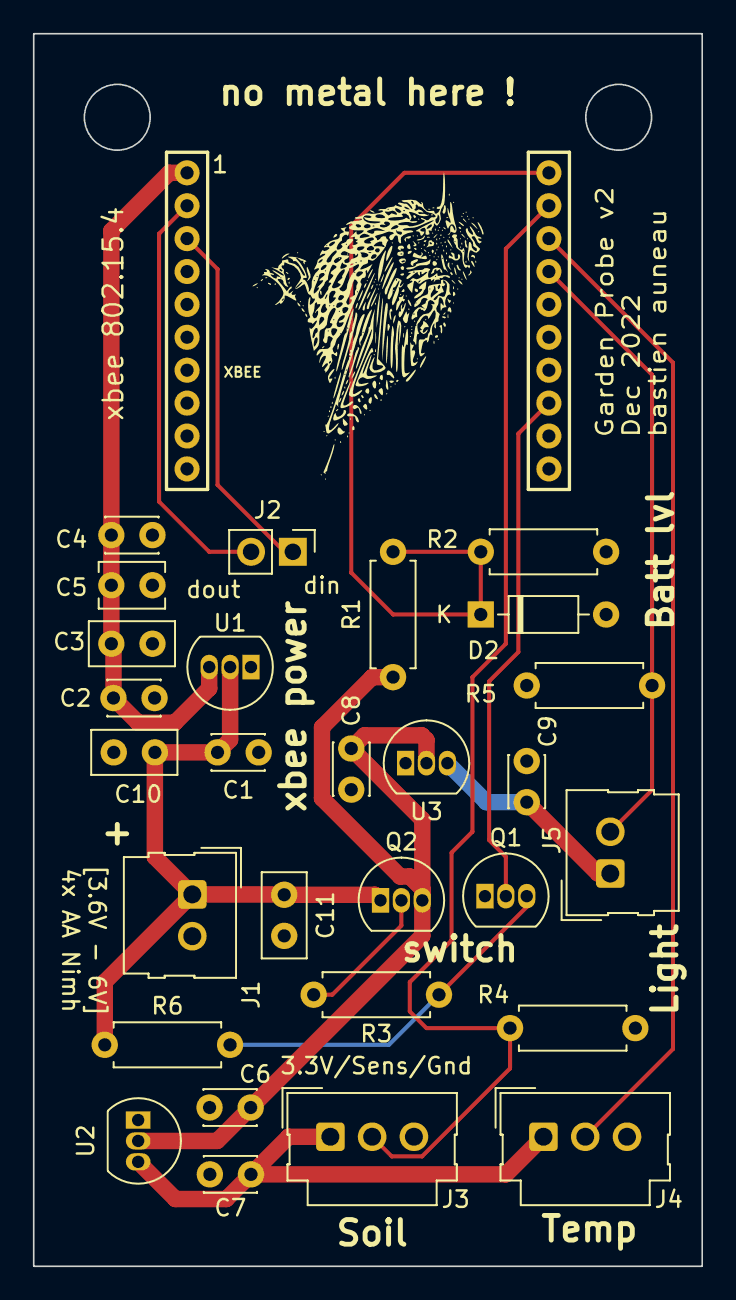
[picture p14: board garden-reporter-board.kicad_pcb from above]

Board: 2 copper layers, 40.6 x 74.9 mm, 29 parts (0 on the bottom side), 15 nets.

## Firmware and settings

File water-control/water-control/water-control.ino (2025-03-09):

#include "ball_valve.h"
#include "button.h"
#include "epoch_time_t.h"
#include "led.h"
#include "http_reporter.h"
#include "web_log.hpp"
#include "wifi.h"

// Should not wrap, coz 2^32 * 0.00245 = 10.5 million liters
// ... considering max flow being 10L / minute --> 1 million minute --> 1.9 years of non-stop watering
// ... or 45 years of daily watering for 1 hour (winter included)
uint32_t flow_cnt = 0;
uint32_t flow_cnt_last = 0;
//const float flow_cnt_liter_per_edge = 0.00245;
// Use 1/10 fluid ounce (fl oz), ie 1/10 * 28.4 mL
const float flow_cnt_liter_per_edge = 0.00284;

uint32_t start_water_cnt = 0;
uint32_t start_water_cnt_last = 0;

// Wifi report period
const unsigned int sec_report_period = (15 * 60); // TODO 15 min
// local clock of last report, or invalid if previously failed
epoch_time_t last_report_ = -1;
const unsigned int sec_report_period_when_watering = 60;
const unsigned int water_loop_period_sec = 5;

// Hard limit watering duration, 1.5 hour
const int64_t MAX_WATER_DURATION_SEC = 5400;

// delay between loop
const unsigned int millisec_loop_step = (200);

// Twice report period, to avoid missing first watering
// 20 min minimum !
const epoch_time_t water_schedule_margin_sec = max(sec_report_period * 2, 20 * 60);

epoch_time_t next_water_schedule;
epoch_time_t last_water_schedule;

void flow_trig_isr()
{
  flow_cnt ++;
}

button_t button;
epoch_time_sync_t epoch_time_sync;
led_t led(&epoch_time_sync);
web_log_t web_log;
ball_valve_t ball_valve;
wifi_t wifi;
http_reporter_t reporter;

// Command received by server
http_reporter_t::command_t server_cmd;

// Log tp serial/usb
#define LOG(X) ({ \
  Serial.print(epoch_time_sync.now_as_string()); \
  Serial.print(" - "); \
  Serial.print(X); \
})

// Log with a timestamp to web server. Send unix time as hex string
#define WEB_LOG(STR) ({ \
  epoch_time_t now = epoch_time_sync.now(); \
  web_log.append(String((uint32_t)(now >> 32), HEX)); \
  web_log.append(String((uint32_t)(now & 0xffffffff), HEX) + " "); \
  web_log.append(STR); \
  web_log.commit(); \
})

void setup()
{
  // debug
  Serial.begin(115200);
  Serial.println("--");
  Serial.println("-- setup");

  pinMode(FLOW_TRIG, INPUT_PULLUP);
  attachInterrupt(
    digitalPinToInterrupt(FLOW_TRIG), flow_trig_isr, FALLING
  );
  
  epoch_time_sync.init();
  button.init();
  led.init();
  ball_valve.init();

  // Suspecting low power sleep to make USB serial unstable !!!
  // |--> confirm later, use normal delay/interrupt for now

  // blink
  led.blink(3, 1000, 50);
  
  // Debug
  pinMode(LED_BUILTIN, OUTPUT);

  // Avoid false positive on startup
  // (only happens when plug/unplug, not when using arduino reset button)
  button.reset_start_water_push();

  Serial.println("--");
  Serial.println("-- setup END");

  WEB_LOG("Setup END");
}


/**
 * @warning Expects Wifi to be connected !
*/
report_status sync_with_server(bool allow_clock_adjust)
{
  report_status rs = report_status::FAILURE;
  
  // Compute water since last successful report
  int32_t flow_cnt_tmp = flow_cnt;
  float water_liter = (float)(flow_cnt_tmp - flow_cnt_last) * flow_cnt_liter_per_edge;

  http_reporter_t::command_t cmd = reporter.report(
    water_liter,
    0,
    next_water_schedule,
    server_cmd.enabled,
    last_water_schedule,
    ball_valve.is_on(),
    epoch_time_sync.uptime_sec(),
    wifi.rssi_dbm(),
    epoch_time_sync.rtc_temp_celsius(),
    &web_log
  );
  
  if (cmd.is_valid)
  {
    // report was succesful, reset flow cnt last
    flow_cnt_last = flow_cnt_tmp;

    if (allow_clock_adjust)
    {
      int offset_applied = epoch_time_sync.set_now(cmd.sec_since_epoch);
      if (offset_applied != 0)
      {
        WEB_LOG(String("Adjusted RTC clock by ") + offset_applied + String(" seconds"));
      }
    }

    if (server_cmd == cmd)
    {
      //Serial.println("--> Ignore server command, already known");
      rs = report_status::CMD_ALREADY_KOWN;
    }
    else
    {
      server_cmd = cmd;
      LOG("--> Apply server command");
      Serial.println("");
      WEB_LOG("Apply new schedule from server");
      // A config has been received from server
      // ensure next scheduled water is in the future
      next_water_schedule = server_cmd.start_time_sec_since_epoch;
      while(next_water_schedule < epoch_time_sync.now() - water_schedule_margin_sec)
      {
        next_water_schedule += server_cmd.period_day * 24 * 60 * 60;
      }
      Serial.print("    Next watering at ");
      Serial.println(next_water_schedule);
      Serial.print("    happening in sec: ");
      Serial.println(next_water_schedule - epoch_time_sync.now());
      rs = report_status::CMD_APPLIED;
    }
  }
  return rs;
}

void water_for_duration(int32_t duration_sec, bool is_manual_triggered)
{
  if (duration_sec > MAX_WATER_DURATION_SEC)
  {
    duration_sec = MAX_WATER_DURATION_SEC;
  }

  epoch_time_t deadline = epoch_time_sync.now() + duration_sec;

  LOG(" >> Water NOW << duration minutes: ");
  Serial.println((float)duration_sec / 60.0);
  String manual_suffix = "";
  if (is_manual_triggered)
  {
    manual_suffix = " (manual trigger)";
  }
  WEB_LOG(String(">> Water for ") + (int)(((float)duration_sec / 60.0) + 0.5) + String(" minutes") + manual_suffix);
  //digitalWrite(LED_BUILTIN, HIGH);

  ball_valve.water_on();

  // Report on first iteration
  epoch_time_t http_report_deadline = epoch_time_sync.now();

  // Report as long as it is watering
  // ... and check if config get changed
  while(epoch_time_sync.now() < deadline)
  {
    // Cancel if button is off
    if (button.allow_water() == false)
    {
      LOG("Cancel watering, by order of button");
      Serial.println("");
      WEB_LOG("Cancel watering, by order of button");
      break;
    }
    if (wifi.is_connected() && epoch_time_sync.now() >= http_report_deadline)
    {
      // HTTP report
      led.on();
      report_status rs = sync_with_server(false);
      // manual triger ignores water schedule enable/disable
      if ( !is_manual_triggered && rs == report_status::CMD_APPLIED)
      {
        // Check enabled only to interrupt the loop
        // other config were applied in sync_with_server()
        if (server_cmd.enabled == false)
        {
          LOG("Cancel scheduled watering, by order of server");
          Serial.println("");
          WEB_LOG("Cancel scheduled watering, by order of server");
          break;
        }
      }
      http_report_deadline = epoch_time_sync.now() + sec_report_period_when_watering;
      led.off();
    }
    // fade also means delay
    led.fade(water_loop_period_sec, 1000);
  }

  ball_valve.water_off();

  LOG(" >> STOP Water <<");
  Serial.println("");
}


void loop()
{
  //// HTTP report ////
  // Send status and get config including epoch time sync and watering schedule
  if (last_report_ < 0 || (epoch_time_sync.now() - last_report_ > sec_report_period))
  {
    // Report via wifi
    led.on();
    if (wifi.connect())
    {
      report_status rs = sync_with_server(true);
      if (CMD_APPLIED == rs)
      {
        // Sync with success
        // received a new config, re-report to update status
        sync_with_server(true);
      }
      else if (FAILURE == rs)
      {
        // Also update timestamp, to avoid fast re-try
        // ... which may happen if server or net is down
        LOG("[!] Failed periodic sync with server !!");
      }
      last_report_ = epoch_time_sync.now();
    }
    // Regardless of success or not, turn off Wifi
    wifi.end();
    led.off();
  }

  //// Water schedule ////
  if (server_cmd.is_valid)
  {
    // Perfom scheduled watering
    // If water isn't allowed/enabled still do update next watering coz it has passed
    if (epoch_time_sync.now() > next_water_schedule)
    {
      led.on();
      wifi.connect();
      if (button.allow_water() && server_cmd.enabled)
      {
        water_for_duration(server_cmd.duration_minute * 60, false);
      }
      else
      {
        // First arg should be String, so other operands can be auto-cast to String
        WEB_LOG(String("Scheduled water skipped button:") + button.allow_water() + " web enabled:" + server_cmd.enabled);
      }

      // Re-schedule
      // ... but not if it has been re-scheduled by wifi config already
      // ... meaning next schedule is not already set in future
      if (epoch_time_sync.now() > next_water_schedule)
      {
        last_water_schedule = next_water_schedule;
        next_water_schedule += server_cmd.period_day * 24 * 60 * 60;
        LOG("Next watering at ");
        Serial.println(next_water_schedule);
        Serial.print("  happening in sec: ");
        Serial.println(next_water_schedule - epoch_time_sync.now());
        WEB_LOG("Re-schedule next water");
      }
      // report to update status
      if (wifi.is_connected())
      {
        sync_with_server(false);
      }
      // Regardless success or not, need to turn off Wifi
      wifi.end();
      led.off();
    }
  }

  if (button.start_water_was_pushed())
  {
    if (button.bit_value() == 0)
    {
      // trigger report to HTTP server on next iteration
      LOG("-- Manual trigger HTTP report");
      last_report_ = -1;
    }
    else
    {
      LOG("-- Manual trigger water");
      // check button on/off
      if (button.allow_water())
      {
        led.on();
        wifi.connect();
        
        // multiple of 15 minutes
        uint32_t duration_sec = button.bit_value() * 15 * 60;
        water_for_duration(duration_sec, true);
        
        // trigger report to HTTP server on next iteration
        last_report_ = -1;
        
        wifi.end();
        led.off();
      }
      else
      {
        // First arg should be String, so other operands can be auto-cast to String
        WEB_LOG(String("Manual water skipped button:") + button.allow_water());
      }
    }
    button.reset_start_water_push();
  }

  delay(millisec_loop_step);
}

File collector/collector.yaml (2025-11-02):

---
  xbee:
    port: "/dev/ttyUSB0"
    baudrate: 115200

  serial-tcp:
    host: 0.0.0.0
    port: 8087

  influxdb:
    hostname: "http://localhost:8086"
    measurement: 
      probe: "jardin-pa-bakken"
      water-web-control: "water-web-control"
      probe-calibration: "jardin-pa-bakken-calibration"

  probes:
    - name: "Unit #1"
      id: 0x0013A20041CF2184
      location: "potager sud"
      calibration: false
      battery:
        v-divider: 6.0
      soil-moisture:
        # got 56 inside, then outside around 80 (been moving probe)
        # is it really related to in/out condition ?
        # With 56, seen 101% humidity --> 50
        # With 50, seen 104% --> use 30
        immerged-value: 30
        dry-value: 546
      temperature:
        coef: 0.1173
        offset: -50.0
      light:
        # 95.8 = 1.2 / 1023.0 / light_R (68) * 100000.0 / 0.018
        # gives max 98039
        # scale to probe #2 220 ~= 95.8 * 2.3 
        #coef: 408.1 # looks too high coz always double of Nord
        coef: 200.0
        offset: 0
    - name: "Unit #2"
      id: 0x0013A20041ECE6E8
      location: "noisetier"
      battery:
        v-divider: 6.0
      soil-moisture:
        # calibration gave 584
        # but calib of #3 went from 625 to 600 after 1 night
        # This could explain that noisetier has unexpected high humidity ?
        # Trying to lower proportionally : 600 * 584 / 625 ~= 560
        # --> must be due to outside temp, see below
        # About temp, it probably has a much greater impact when out in the air
        # meaning if calibrating in plain sun
        # --> calibrate in shadow, avoid hot days
        # also found blisters on moisture probe, patched edges with nail polish
        # dry: 887
        immerged-value: 560
        # 903
        # re-calibrate 21/05/2023 : 897
        dry-value: 897
        disabled: true
      temperature:
        coef: 0.1173
        offset: -50.0
      light:
        coef: 60.7
        offset: 0
    - name: "Unit #3"
      id: 0x0013A20041CF2186
      #id: 0x0013A20041F25755
      location: "potager nord"
      calibration: false
      battery:
        v-divider: 6.0
      soil-moisture:
        # just trial and error, assuming that when raining heavily, values should converge
        immerged-value: 41
        dry-value: 595
      temperature:
        coef: 0.1173
        offset: -50.0
      light:
        coef: 60.6
        offset: 0
    - name: "Unit #4"
      id: 0x0013A200420821EB
      location: "maison"
      battery:
        v-divider: 6.0
      soil-moisture:
        # dummy
        immerged-value: 0
        # dummy
        dry-value: 0
        disabled: true
      temperature:
        coef: 0.1173
        offset: -50.0
      # TODO
      light:
        coef: 1.068
        offset: -79.0

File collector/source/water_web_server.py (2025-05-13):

from http.server import ThreadingHTTPServer, BaseHTTPRequestHandler
import re, json, time
from datetime import datetime, timedelta
import urllib.parse
import yaml
import threading
import shutil

# debug/test
import os

CONFIG_BASE_NAME = "water-web-config.yaml"
# template used if no config already present
CONFIG_TEMPLATE = "./" + CONFIG_BASE_NAME
# config, placed in a docker named volume
CONFIG_PATH = "/var/lib/garden-collector/" + CONFIG_BASE_NAME

'''
Logic that handles http requests from the water control unit
And that exposes a simple wep page to set water scheduling (for humans)

When the water control unit awakes, it send a GET request to /report
Which variables : 
 * water counter in Liter
   (could be reset any time to 0)
 * water schedule : 
   - period in days
   - next scheduled start time in sec since EPOCH
   - duration in minute
   - enabled
 * status (Could be all 0 after reboot)
  - sec since last boot
  - last water time in sec since epoch
  - last water duration in minutes
  - next water scheduled time in sec since epoch
  - next water scheduled duration in minutes

The request is answered with a JSON object including :
 * water schedule config : 
   - start time in sec since EPOCH
   - period in days
   - duration in minute
   - enabled

None of the above variables or json entries are guaranteed to be present
'''
class WaterWebRequestHandler(BaseHTTPRequestHandler):
    def log_request(self, code):
        pass

    def do_POST(self):
        url_parsed = urllib.parse.urlparse(self.path)
        
        # human interface
        if url_parsed.path == '/':
            # get config from yaml
            config = self.load_config_file()
            if config != None:
                content_len = int(self.headers.get('Content-Length'))
                post_body = self.rfile.read(content_len)
                #print('post_body', post_body.decode("utf-8"))
                # get POST params, if any
                query_components = urllib.parse.parse_qs(post_body.decode("utf-8"))
                #print('query_components', query_components)
                try:
                    config["water-control"]['start_time'] = query_components.get('start_time')[0]
                    config["water-control"]['period_day'] = int(query_components.get('period_day')[0])
                    config["water-control"]['duration_minute'] = int(query_components.get('duration_minute')[0])
                    config["water-control"]['enabled'] = query_components.get('enable', ['off'])[0] == 'on'
                    print('-->', config)
                    self.write_config_file(config)
                except Exception as e:
                    print('POST data does not contain expected params, ignore it...')
                    print(e)
                
                self.render_index(config["water-control"])
        

    def do_GET(self):
        url_parsed = urllib.parse.urlparse(self.path)

        # human interface
        if url_parsed.path == '/':
            # get config from yaml
            config = self.load_config_file()
            if config != None:
                self.render_index(config["water-control"])
        
        # human interface AJAX
        elif self.path == '/status':
            #print('-- status !')
            self.send_response(200)
            self.send_header('Content-type', 'application/json')
            self.end_headers()
            last_schedule = datetime.fromtimestamp(self.server.valve_status.last_water_epoch_t).strftime('%Y-%m-%d %H:%M')
            water_schedule_enabled = '1'
            if self.server.valve_status.water_schedule_enabled == False:
                water_schedule_enabled = '0'
            next_schedule = datetime.fromtimestamp(self.server.valve_status.next_water_epoch_t).strftime('%Y-%m-%d %H:%M')
            battery_status_string = "{:.0f}% ({:.2f})V".format(
                (float(self.server.valve_status.battery_milliv) / 1000.0 - 3.2) * 100  / 1, 
                float(self.server.valve_status.battery_milliv) / 1000.0
            )
            watering_now_string = 'nope'
            if self.server.valve_status.is_water_on :
                watering_now_string = 'yes'
            uptime_day_value = "{:.2f} days".format(
                float(self.server.valve_status.uptime_sec) / (3600.0 * 24.0)
            )
            last_report = datetime.fromtimestamp(self.server.valve_status.last_report).strftime('%Y-%m-%d %H:%M')
            data = {\
                'last_scheduled_watering': last_schedule,
                'water_schedule_enabled': water_schedule_enabled,
                'next_scheduled_watering': next_schedule,
                'battery_status': battery_status_string,
                'watering_now': watering_now_string,
                'uptime_day': uptime_day_value,
                'last_report': last_report,
                'weblog': self.server.valve_status.weblog
            }
            #print("Sending: ", data)
            json_data = json.dumps(data)
            self.wfile.write(json_data.encode())
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

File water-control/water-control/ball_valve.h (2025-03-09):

#pragma once

#include "pin.h"

// Set Driver phase, WARNING RISK of inverse polarity !!
// Looking at arduibox, left is GND, right is +15V
// Note: Been seeing some strange behavior with polarity/phase
//       as if polarity was stuck regardless of phase
//       But then it was opposite than what was measured without load
//       |--> could it be that proper measure need load ?
#define BALL_VALVE_POLARITY LOW

#define BALL_VALVE_ON HIGH
#define BALL_VALVE_OFF LOW

/**
* Controle DRV8874 Single Brushed DC Motor Driver Carrier
* Which is used as a driver a ball valve
* mini board : https://www.pololu.com/product/4035
* It uses 2 PIN to control
* Enable | Phase | OUT1 | OUT2 |
* ------------------------------
*    0   |   X   |   L  |  L   |
* ------------------------------
*    1   |   1   |   H  |  L   |
* ------------------------------
*    1   |   0   |   L  |  H   |
* ------------------------------
* Ball valves is closed by default
* It opens when applying DC 9-24V
* and remains open until DC is removed
* @WARNING WRONG PHASE means REVERSE POLARITY !!
*/
struct ball_valve_t
{
  /**
   * @param flow_cnt_ptr pointer to flow pulse counter, to check that water flows or not
  */
  void init()
  {
    pinMode(VALVE_ENABLE, OUTPUT);
    digitalWrite(VALVE_ENABLE, BALL_VALVE_OFF);
    pinMode(VALVE_PHASE, OUTPUT);
    digitalWrite(VALVE_PHASE, BALL_VALVE_POLARITY);
  }

  void water_on() 
  {
    // phase is fixed, coz we want fixed polarity
    digitalWrite(VALVE_PHASE, BALL_VALVE_POLARITY);
    digitalWrite(VALVE_ENABLE, BALL_VALVE_ON);
    is_on_ = true;
  }

  bool water_off()
  {
    // phase is fixed, coz we want fixed polarity
    digitalWrite(VALVE_PHASE, BALL_VALVE_POLARITY);
    digitalWrite(VALVE_ENABLE, BALL_VALVE_OFF);
    is_on_ = false;
  }

  bool is_on() const
  {
    return is_on_;
  }

private:
  bool is_on_{false};
};

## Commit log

2022-08-12 Initial commit, removed previous history which was bloated with kicad backup and cache files
    [garden-reporter-board.kicad_pcb, garden-reporter-board.kicad_sch, power_use.ods]
2022-08-21 Feature/probe pcb edge and routing
    [garden-reporter-board.kicad_pcb]
2022-08-21 Smaller mouting holes
    [garden-reporter-board.kicad_pcb]
2022-08-22 Fix bad flyback diode connection, move xbee edge drawing to fron silkscreen
    [garden-reporter-board.kicad_pcb, garden-reporter-board.kicad_sch]
2022-08-22 Add artichoke picture, add and ùake pretty silkscreen comments
    [garden-reporter-board.kicad_pcb]
2022-08-29 Feature/better doc
    [probe-board-BOM.ods, probe-board-power-use.ods]
2022-09-06 Start collector, re-organize folders
    [garden-reporter-board.kicad_pcb, garden-reporter-board.kicad_sch, probe-board-BOM.ods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]
2022-09-24 Feature/v divider for sensors
    [garden-reporter-board.kicad_pcb, garden-reporter-board.kicad_sch, probe-board-power-use.ods]
2022-09-24 Fix Xbee frame decoder bug, started SerialHub, add doc on xbee range
    [collector.py, serial_hub.py]
2022-09-24 Install pyyaml, load probes calib from yaml, and serial config and influxdb config from yaml too
2022-10-03 Use 64 bit ADC frame (x82)
2022-10-12 Basic blocks decoding frames to dict, empty shell with interface for...
2022-10-12 TcpListerner has ref to xbee popo model, fix socat call on tcp client script
    [collector.py, serial_tcp_client.py, tcp_listener.py]
2022-10-12 SerialHub 1 thread to read and one to write, using blocking call for minimal CPU use
2022-10-12 socket accept blocking call and cancel with shutdown()
2022-10-13 Use 1 thread to read 1 to write in TCP Listener, remove some traces
2022-10-16 TODOs and docs on V-divider for light sensor
    [garden-reporter-board.kicad_sch]
2022-10-31 Docker working, update doc, fix showing all past errors on startup
    [xbee_population_model.py]
2022-10-31 Add to light sensor V reg to 1.2V, adjust light R properly, fix layout accordingly
    [garden-reporter-board.kicad_pcb, garden-reporter-board.kicad_sch]
2022-10-31 Comment on soil moisture sensor and V-divider
    [garden-reporter-board.kicad_sch]
2022-11-10 Fix trace bug
2022-11-11 Working state ! Just pulling ADC once, been hacking model, and tuning sleep values
2022-11-13 Xbee population model is executed by collector thread, hack message flow to only sample ADCs
2022-11-14 Poll errors when timeout occrs (24h), write error to db when there is, cleanup
    [influxdb_writer.py, serial_hub.py, xbee_population_model.py]
2022-11-14 Update last error timestamp when recv error msg
    [xbee_population_model.py]
2022-11-15 Fix voltage output range of soil moist sensor, 1.2V to light sensor
    [garden-reporter-board.kicad_pcb, garden-reporter-board.kicad_sch]
2022-11-15 Fix crash and clean README
    [collector.py]
2022-11-17 Fix xbee not being released from config (ie not back to cycle sleep), due to population model being called only when frame is received. Now executing population model on frame RX timeout
    [collector.py, data_calibrator.py, xbee_population_model.py]
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2022-11-18 Use ax+b to calibrate temp
2022-11-28 More profile and dashbord backup
    [garden-reporter-board.kicad_pcb]
2022-12-09 Fix bug on TCP server when bad connection happen
    [tcp_listener.py]
2022-12-12 Better msg, dummy mac for 1s device
2022-12-14 Smaller profile. Re-number sensor mosfet pins properly
    [garden-reporter-board.kicad_pcb, garden-reporter-board.kicad_sch]
2022-12-18 Print frame received out of awakening, remove extra frame sent after awakening
2022-12-18 Add ceriamic cap for xbee and heavy load sensors, better routing of voltage regulator capacitors, more compact outline
    [garden-reporter-board.kicad_pcb, garden-reporter-board.kicad_sch]
2022-12-18 Also pull xbee for supply level, every time CC error is pulled, ie every 24h
    [influxdb_writer.py, xbee_frame_decoder.py, xbee_population_model.py]
2022-12-18 Routing decouple cap
    [garden-reporter-board.kicad_pcb]
2022-12-18 Fix bug and Better message on influx-db error
    [influxdb_writer.py, xbee_population_model.py]
2022-12-23 Use high side switch, chose new components and footprints, layed out but no route, use GND plane, add doc and datasheet
    [garden-reporter-board.kicad_pcb, garden-reporter-board.kicad_sch]
2022-12-23 Route all
    [garden-reporter-board.kicad_pcb, probe-board-BOM.ods]
2022-12-24 Finish and verifiy routing, finish and verify BOM
    [garden-reporter-board.kicad_pcb, garden-reporter-board.kicad_sch, probe-board-BOM.ods]
2022-12-24 Add garden probe v2 gerber files
    [garden-reporter-board-B_Cu.gbr, garden-reporter-board-B_Mask.gbr, garden-reporter-board-B_Silkscreen.gbr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]
2023-02-07 High side switch working fine, fix few comments
    [garden-reporter-board.kicad_sch]
2023-02-07 Notes taken while investigating before going for high side switch
2023-02-07 Translate light ADC read into Lux
2023-02-08 Use v2 config for battery v divider, soil read range, default temperature formula
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2023-02-14 Add R config to light sensor
2023-02-26 Calibrate noisetier
2023-04-03 Lower immerged value probe 1
2023-05-18 Unit #3 and more calibration
2023-05-21 New moist calibration for noisetier and potager nord
    [collector.yaml]
2023-07-29 Better alignment of probe doc
2023-08-09 basic http GET and basic valve control
2023-08-15 Doc on power use. Basic buttons working. Add TimeLib simplified biiig time, better interface
2023-09-03 Add battery.h and solenoid datasheet
2023-09-03 Test mode and doc on pin numbering vs arduibox
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2023-11-25 Fix end point profile, doc
    [serial_tcp_client.py]
2023-11-29 Better light calibration for indoor unit
2024-06-08 Battery, buttons, time sync, report all work
2024-06-11 Schedule can be config from WEB UI, and propagates to arduino. Arduino reports voltage and water volume
2024-06-14 Better epoch sync, clean up, start bringing real status of arduino to web UI
2024-06-14 time sync working like a charm, use msec counter to avoid stacking up rounding errors
    [epoch_time_t.cpp, water-control.ino]
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2024-06-15 Report valve status, count wraps to provide uptime
2024-06-15 Refresh status every 10 sec using AjAX, clean up and minor fixes
    [water_web_server.py]
2024-06-16 Longer valve pulse (1sec), longer max duration (1.5h), check allow water button when schedule watering, led off fix
    [water-control.ino]
2024-06-18 Calibrate water counter, remove debug traces, use Threading HTTP server, count sum of drifts
    [button.h, epoch_time_t.cpp, water-control.ino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]
2024-06-21 Many bug fixes (re-schedule, led, time sync, http response wait
    [epoch_time_t.cpp, water-control.ino, water_web_server.py]
2024-06-24 Write water web control volume and battery in db
2024-06-26 Report when water triggered manually, use RTC clock coz millis() drift wayyyy to much
    [epoch_time_t.cpp, water-control.ino]
2024-06-26 Use named volume for water-web-control config, fix docker files rights, write water usage in db
    [collector.py, influxdb_writer.py, water_web_server.py]
2024-06-26 Remove some print in water web server
2024-06-26 Fix last report bug when config not applied
    [water-control.ino]
2024-07-02 Avergae read battery, adjust safe limit
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2024-07-02 Check battery while watering, fix bug where HTTP report happens all the time when server is down
    [water-control.ino]
2024-07-05 Revert server IP to .66 and sleep duration to 15min
    [water-control.ino]
2024-07-05 Add gerber used to generate v2 PCB, kicad update to v 7.0
2024-07-08 More WEB_LOG for manual trigger and/or watering being skipped, prettify too
    [water-control.ino]
2024-07-11 Notes on soil moisture sensor (new sensor, extra R)
2024-07-12 Add calibration mode, all config yaml are now in a named volume, delay sampling until new soil moisture sensor has settled
2024-08-14 Edit grafana JSON dashboards with updated bucket name
2024-08-14 More comments on pulse length, disabled water on/off retries and init with multiple off. Wires are soldered, current pulse is working fine for 5 tries. Checkpoint before getting pulse secured once an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
2024-08-14 Add scripts to compile/upload/serial to arduino from local
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2025-03-08 Update doc about new 15V power supply and ball valve
2025-03-08 valve_t is now ball_valve_t, ni more pulses and retry and flow feedback
2025-03-09 Valve polarity set, do update ball valve status
2025-03-09 Comment out frame id logic with xbee (continuity counter)
2025-03-09 Docs, small fixes for deploy/docker compose, update main dashboard
    [influxdb_writer.py]
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
